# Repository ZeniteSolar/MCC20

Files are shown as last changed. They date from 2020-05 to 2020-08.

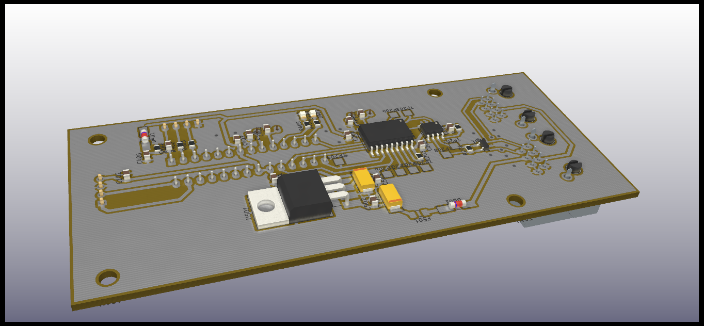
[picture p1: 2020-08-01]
hardware/IMG/3DDOWN.png

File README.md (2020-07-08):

# MCC20
**M**ódulo **C**ontrolador de **C**arga 2020  
Embarcação Guarapuvu II  
Equipe Zênite Solar  

### Sobre

Este módulo é responsável por gerenciar o carregamento da bateria e a operação do painel no seu ponto de maxima potencia 

#### Requisitos e Abordagens
1. Encontrar o ponto de maxima potencia (MPP) do painel solar
    - Utilizar a tecnica perturbar e observar (p&o) para achar o MPP
    - Ao iniciar barrer o duty cicle para iniciar no MPP
    - Se a potencia for 0 fazer o barrido novamente 
2. Medir a Potencia do painel
    - Usar um ina826 para medir a tensao do painel
    - Usar um ina240 para medir a corrente do painel
    
3. Eficiencia energetica
    - Indutores
        - Utilizar fios em paralelo para diminuir o *skin effect*
        - Utilizar indutor acoplado (não implementado)
    - Capacitores
        - Utilizar capacitores SMD com baixa ESR
    - Chaves
        - Utilizar snubber para amortecer oscilações e picos de tensão
        - Utilizar chaves com baixa Rdson e rapidas
        - Utilizar conversor sincrono (não implementado)
    - Frequencia
        - Utilizar frequencia que tenha uma boa relação entre perdas nas chaves e volume do onversor
    - Layout
        - Baixa indutancia no braço (entre chaves)
        - Trilhas curtas
    - Snubber
        - Equilibrio entre sobre-tensão nas chaves e potencia dissipada
4. Robustez
    - Chaves em regime seguro
        - Snubber
        - Layout
    - Proteção *under load* (nao implementado)
    - Capacitores em regime seguro
        - Tensao maxima >Vpan+Vbat
    - Tolerancia termica
        - Projetar assumindo que a temperatura ambiente é 50°
    - Layout simples de montar por metodo artesanal (transferencia termica)

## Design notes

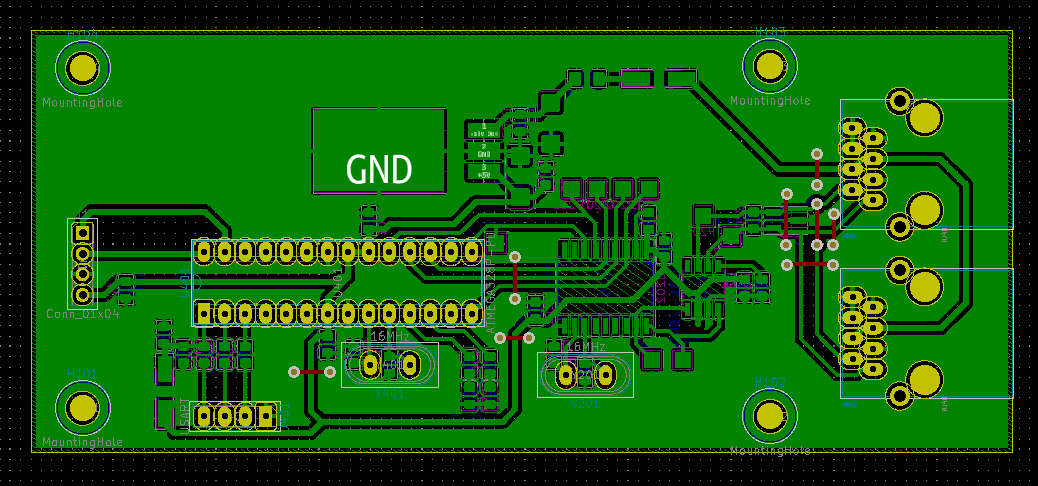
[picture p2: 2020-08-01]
hardware/IMG/layout.png

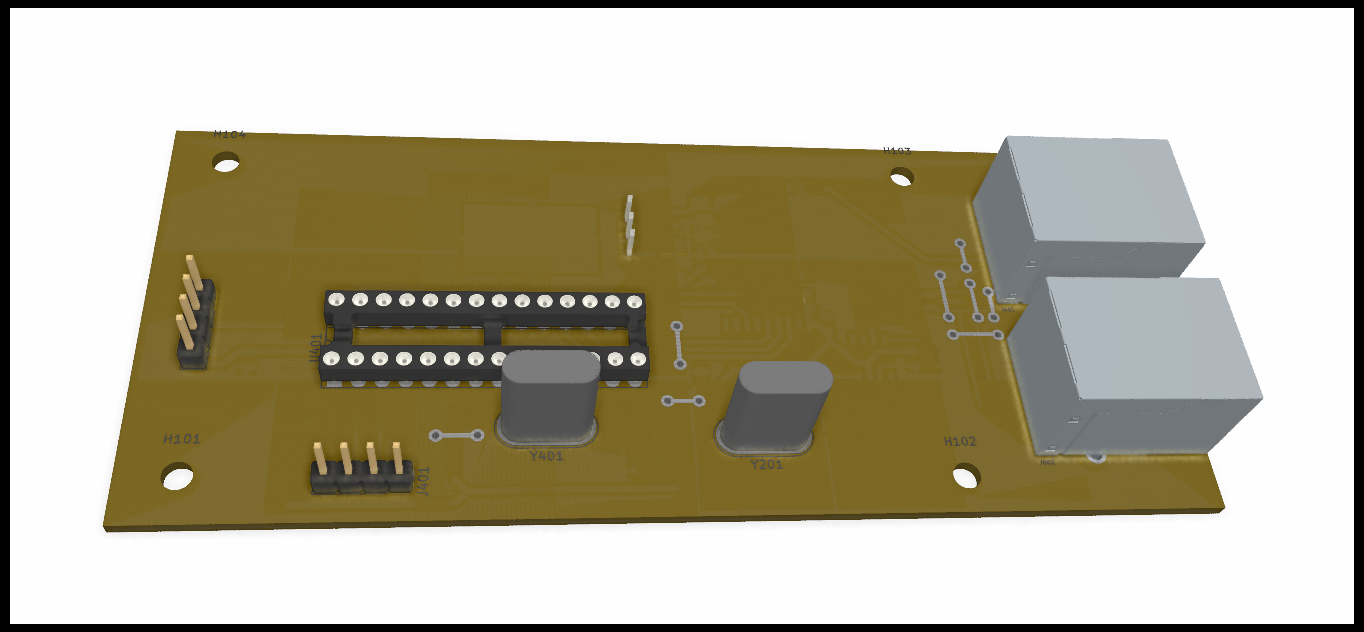
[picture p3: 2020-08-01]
hardware/IMG/3DUP.png

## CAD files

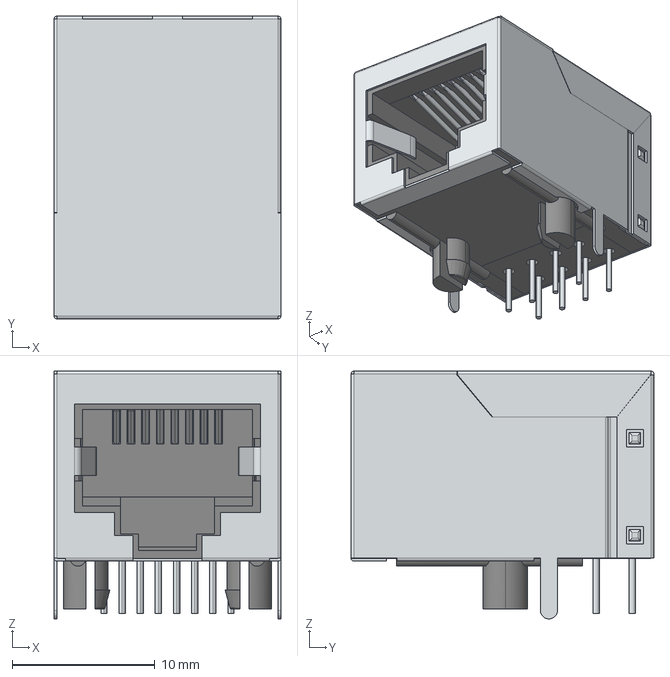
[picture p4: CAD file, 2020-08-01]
hardware/rj45.step
15.9 x 21.2 x 17.3 mm

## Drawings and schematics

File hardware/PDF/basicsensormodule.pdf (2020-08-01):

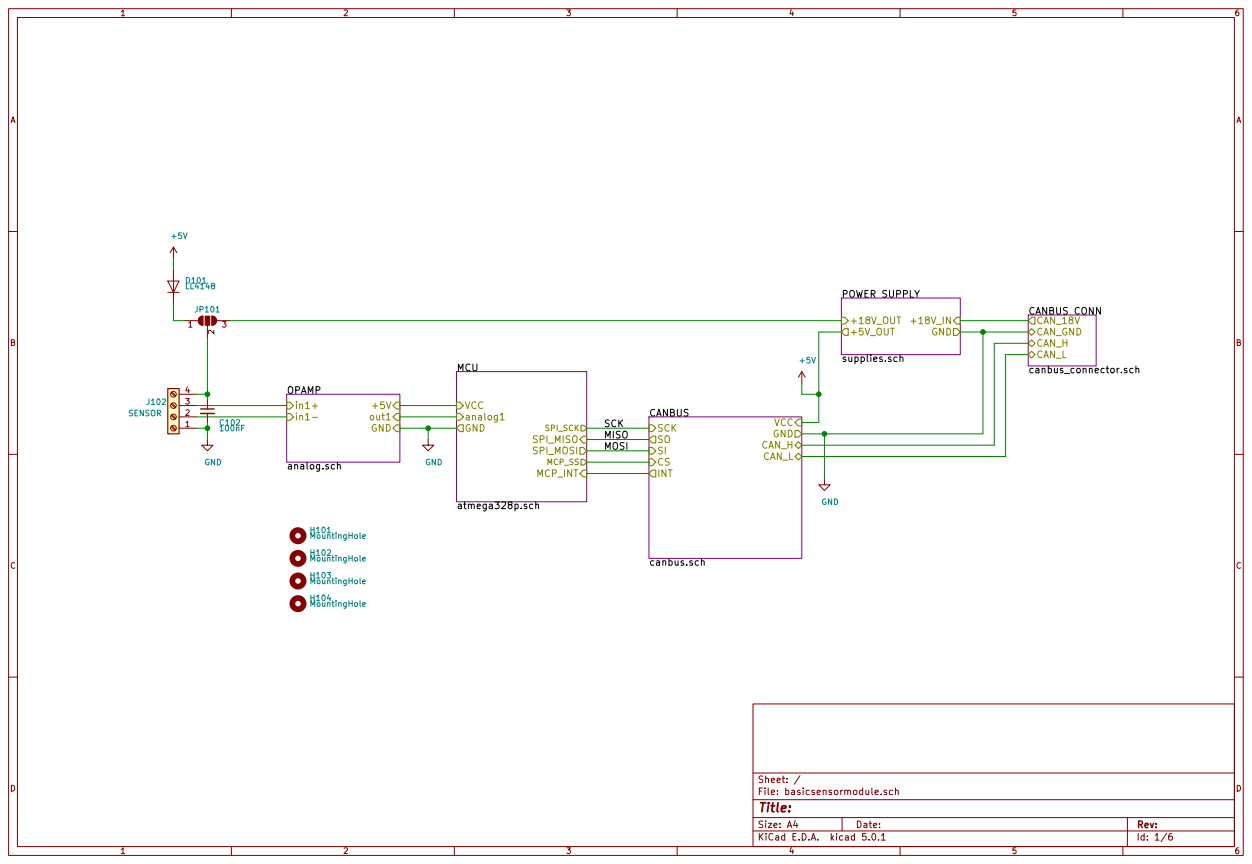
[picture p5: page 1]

Id: 1/6 Title: File: basicsensormodule.sch Sheet: / CANBUS
SCK
canbus.sch SI

MISO
MOSI

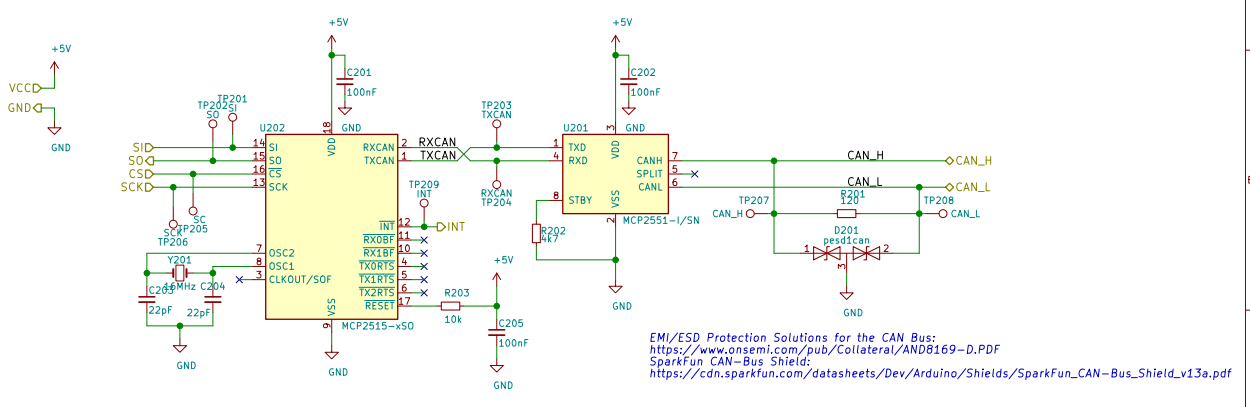
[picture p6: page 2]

https://cdn.sparkfun.com/datasheets/Dev/Arduino/Shields/SparkFun_CAN-Bus_Shield_v13a.pdf TP203 TXCAN

3 RXD 4 SPLIT 5 CANL 6 CANH 7 STBY 8 U201 MCP2551-I/SN TXCAN
RXCAN

EMI/ESD Protection Solutions for the CAN Bus:
https://www.onsemi.com/pub/Collateral/AND8169-D.PDF
SparkFun CAN-Bus Shield:

Id: 2/6 Title: File: canbus.sch Sheet: /CANBUS/

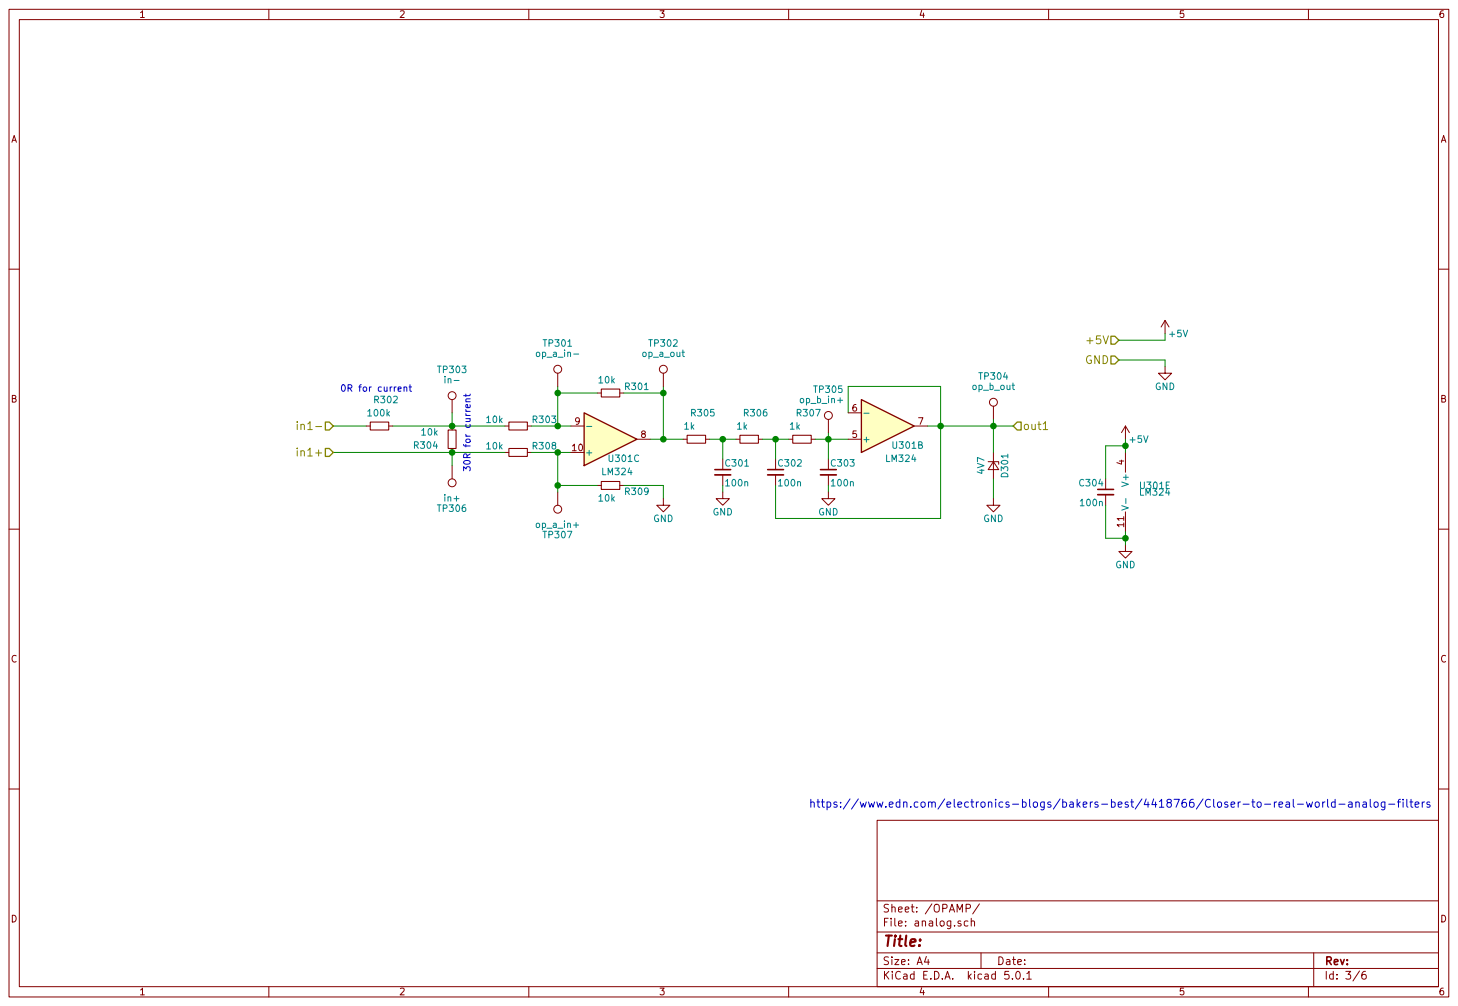
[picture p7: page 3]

https://www.edn.com/electronics-blogs/bakers-best/4418766/Closer-to-real-world-analog-filters R305

File: analog.sch Sheet: /OPAMP/
Id: 3/6 Title:

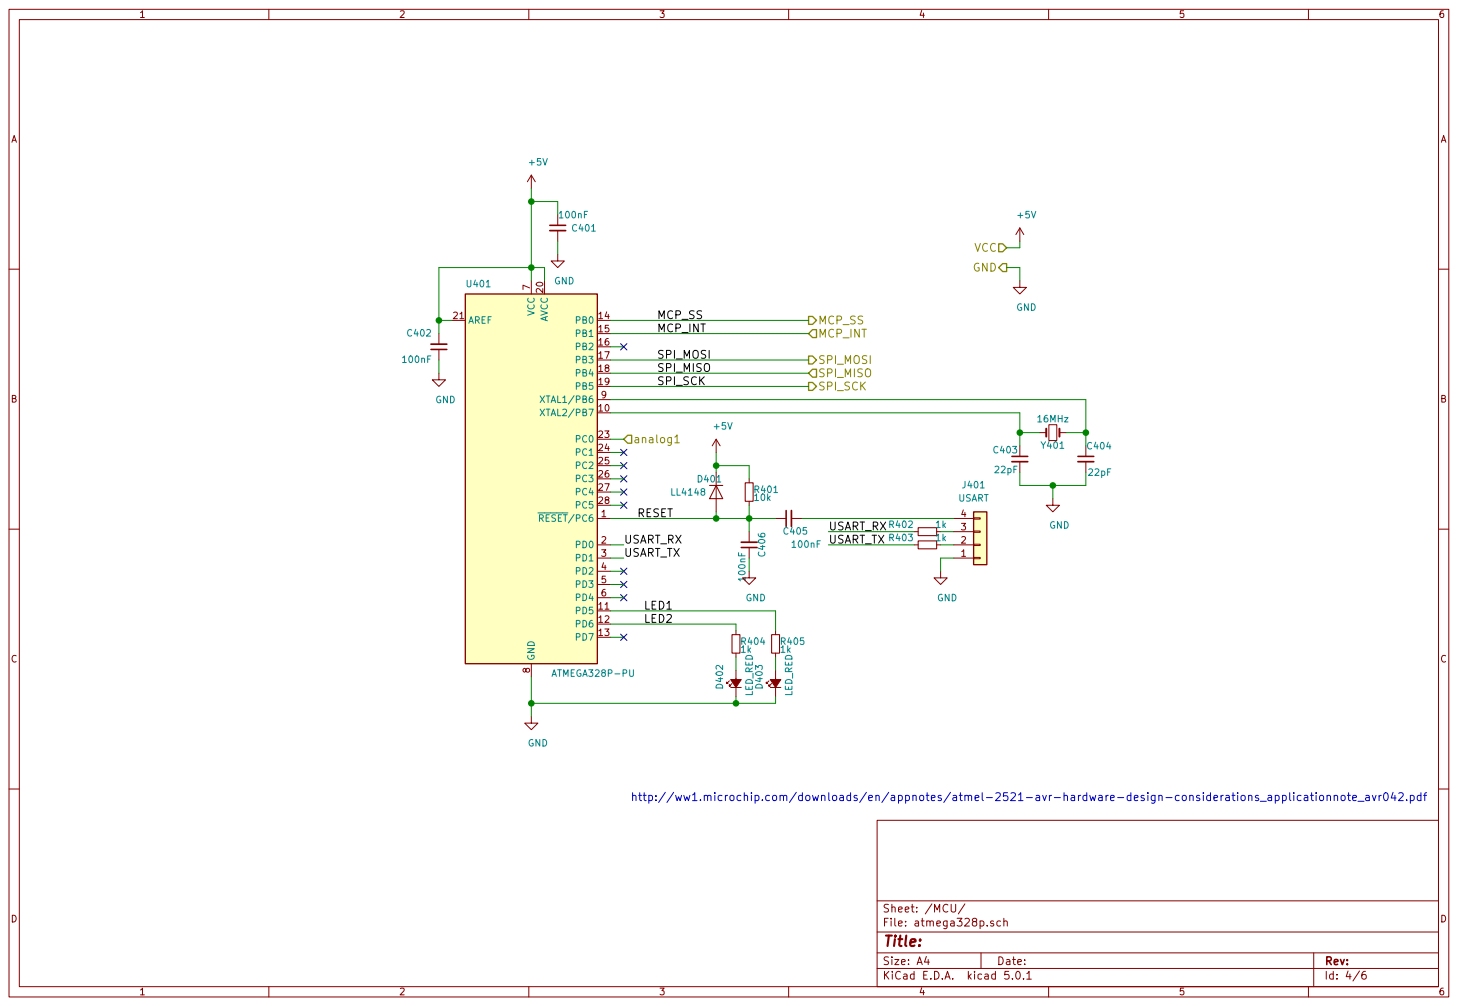
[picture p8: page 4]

File: atmega328p.sch Sheet: /MCU/
Id: 4/6 Title:

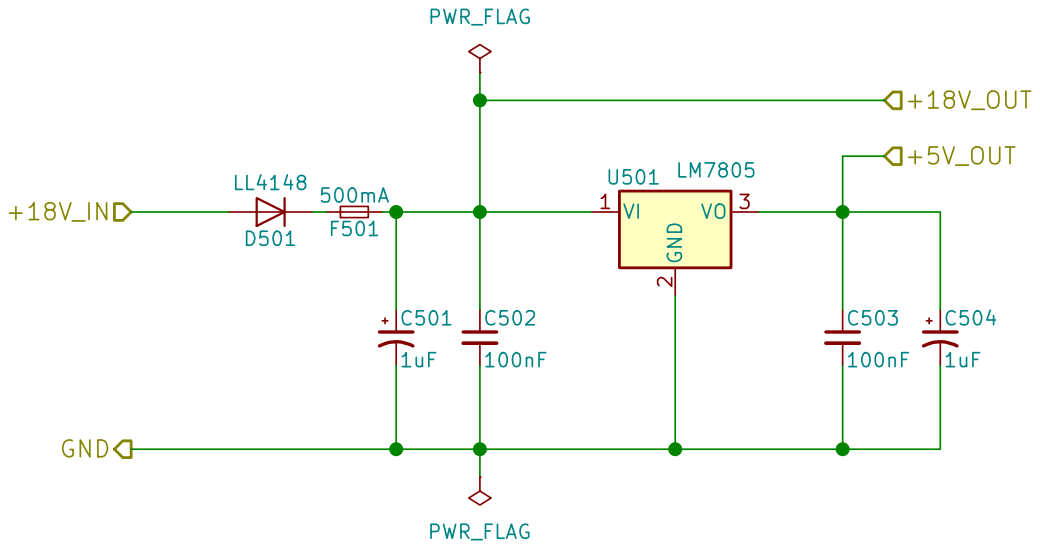
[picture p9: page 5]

File: supplies.sch Sheet: /POWER SUPPLY/
Id: 5/6 Title:

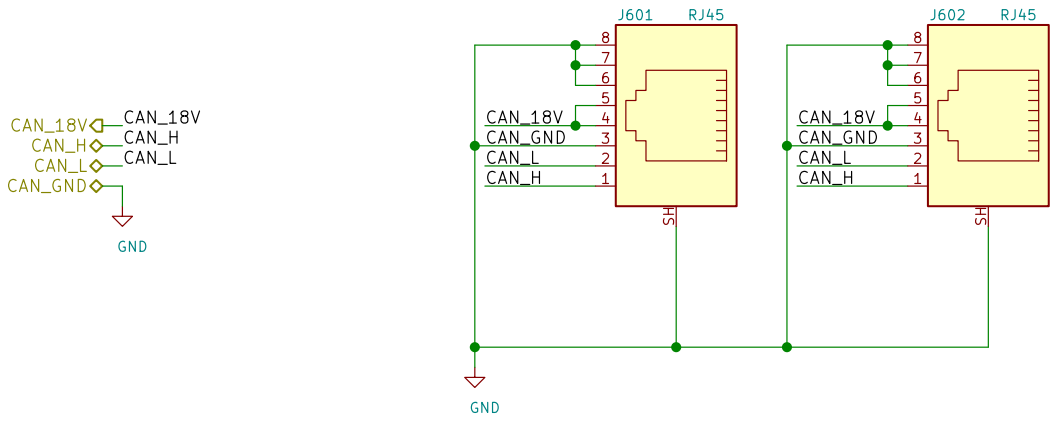
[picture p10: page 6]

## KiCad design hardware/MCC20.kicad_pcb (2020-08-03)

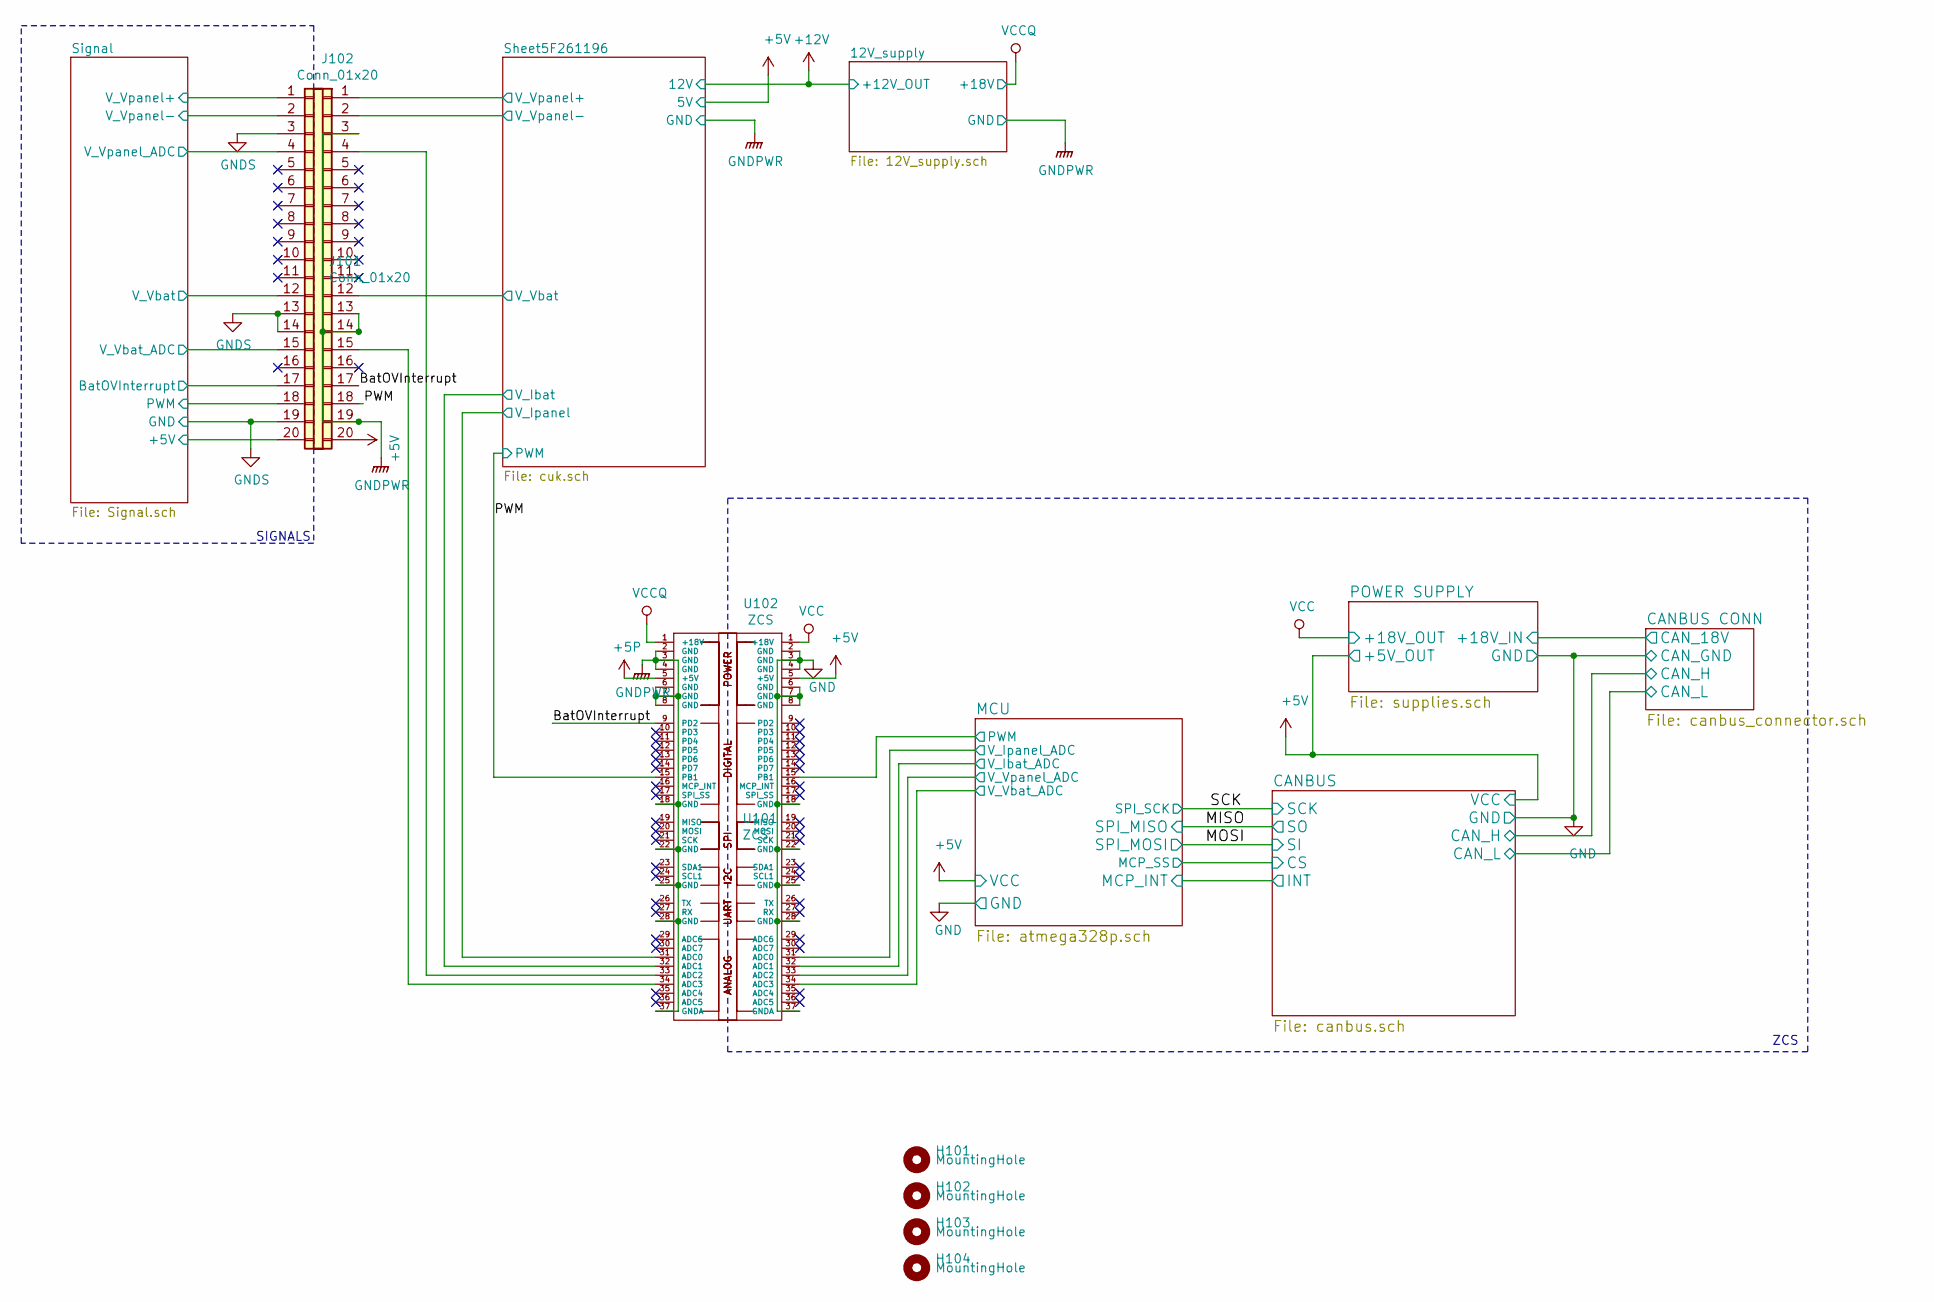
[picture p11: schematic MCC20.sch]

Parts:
H101, H102, H103, H104: MountingHole; MountingHole_3.2mm_M3
J101: Conn_01x20; PinHeader_1x20_P2.54mm_Horizontal
J102: Conn_01x20; PinSocket_1x20_P2.54mm_Vertical_SMD_Pin1Left
U101, U102: ZCS; ZCS18

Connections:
+5P: U101.5 (+5V)
+5V: J102.20, U102.5 (+5V); also elsewhere on the board
+5VA: J101.20; also elsewhere on the board
/BatOVInterrupt: J102.17, U101.9 (PD2)
/MCU/PWM: U102.15 (PB1); also elsewhere on the board
/MCU/V_Ibat_ADC: U102.32 (ADC1); also elsewhere on the board
/MCU/V_Ipanel_ADC: U102.31 (ADC0); also elsewhere on the board
/MCU/V_Vbat_ADC: U102.34 (ADC3); also elsewhere on the board
/MCU/V_Vpanel_ADC: U102.33 (ADC2); also elsewhere on the board
/PWM: J102.18, U101.15 (PB1); also elsewhere on the board
/Sheet5F261196/V_Ibat: U101.32 (ADC1); also elsewhere on the board
/Sheet5F261196/V_Ipanel: U101.31 (ADC0); also elsewhere on the board
/Sheet5F261196/V_Vbat: J102.12; also elsewhere on the board
/Sheet5F261196/V_Vpanel+: J102.1; also elsewhere on the board
/Sheet5F261196/V_Vpanel-: J102.2; also elsewhere on the board
/Signal/BatOVInterrupt: J101.17; also elsewhere on the board
/Signal/PWM: J101.18; also elsewhere on the board
/Signal/V_Vbat: J101.12; also elsewhere on the board
/Signal/V_Vbat_ADC: J101.15; also elsewhere on the board
/Signal/V_Vpanel+: J101.1; also elsewhere on the board
/Signal/V_Vpanel-: J101.2; also elsewhere on the board
/Signal/V_Vpanel_ADC: J101.4; also elsewhere on the board
GND: J102.3, J102.13, J102.14, J102.19, U101.2 (GND), U101.3 (GND), U101.4 (GND), U101.6 (GND), U101.7 (GND), U101.8 (GND), U101.18 (GND), U101.22 (GND), U101.25 (GND), U101.28 (GND), U101.37 (GNDA), U102.2 (GND), U102.3 (GND), U102.4 (GND), U102.6 (GND), U102.7 (GND), U102.8 (GND), U102.18 (GND), U102.22 (GND), U102.25 (GND), U102.28 (GND), U102.37 (GNDA); also elsewhere on the board
GNDA: J101.3, J101.13, J101.14, J101.19; also elsewhere on the board
unnamed: J102.4, U101.33 (ADC2)
unnamed: J102.15, U101.34 (ADC3)
VCC: U102.1 (+18V); also elsewhere on the board
VCCQ: U101.1 (+18V); also elsewhere on the board

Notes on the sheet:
ZCS
SIGNALS

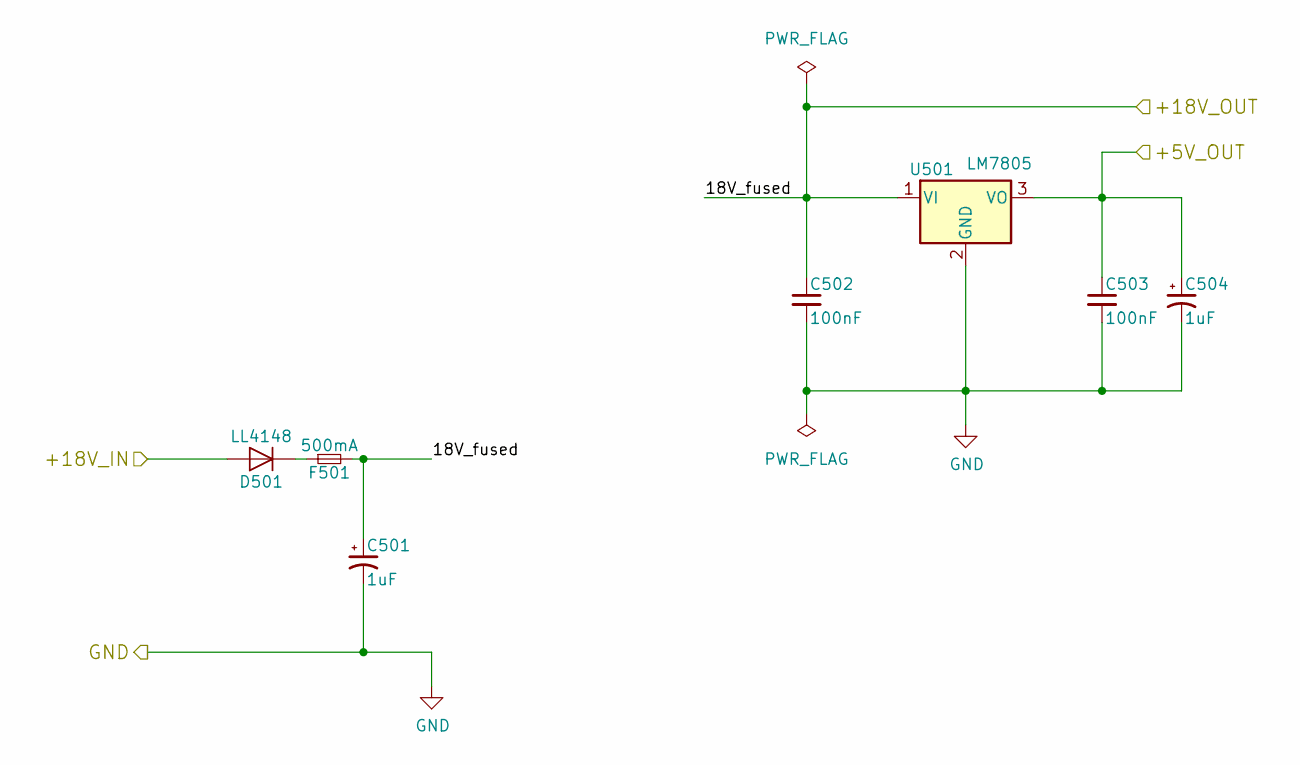
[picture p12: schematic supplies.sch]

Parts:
C501, C504: 1uF; CP_EIA-6032-20_AVX-F_Pad2.25x2.35mm_HandSolder
C502, C503: 100nF; C_0805_2012Metric_Pad1.15x1.40mm_HandSolder
D501: LL4148; D_MiniMELF_Handsoldering
F501: 500mA; Fuse_1206_3216Metric_Pad1.42x1.75mm_HandSolder
U501: LM7805; TO-220-3_Horizontal_TabDown_SMD

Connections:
+5V: C503.1, C504.1, U501.3 (VO); also elsewhere on the board
/POWER SUPPLY/+18V_IN: D501.2 (A); also elsewhere on the board
GND: C501.2, C502.2, C503.2, C504.2, U501.2 (GND); also elsewhere on the board
unnamed: D501.1 (K), F501.1
VCC: C501.1, C502.1, F501.2, U501.1 (VI); also elsewhere on the board

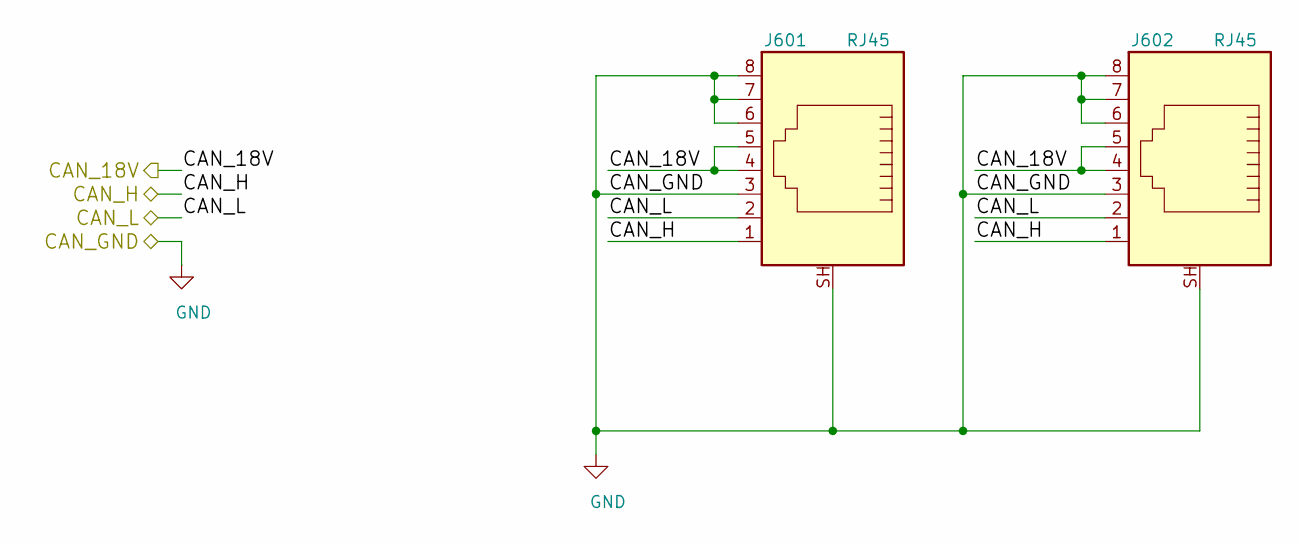
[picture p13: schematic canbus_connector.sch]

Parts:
J601, J602: RJ45; RJ45_YH59_01

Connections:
/CANBUS CONN/CAN_H: J601.1, J602.1; also elsewhere on the board
/CANBUS CONN/CAN_L: J601.2, J602.2; also elsewhere on the board
/POWER SUPPLY/+18V_IN: J601.4, J601.5, J602.4, J602.5; also elsewhere on the board
GND: J601.3, J601.6, J601.7, J601.8, J601.SH, J602.3, J602.6, J602.7, J602.8, J602.SH; also elsewhere on the board

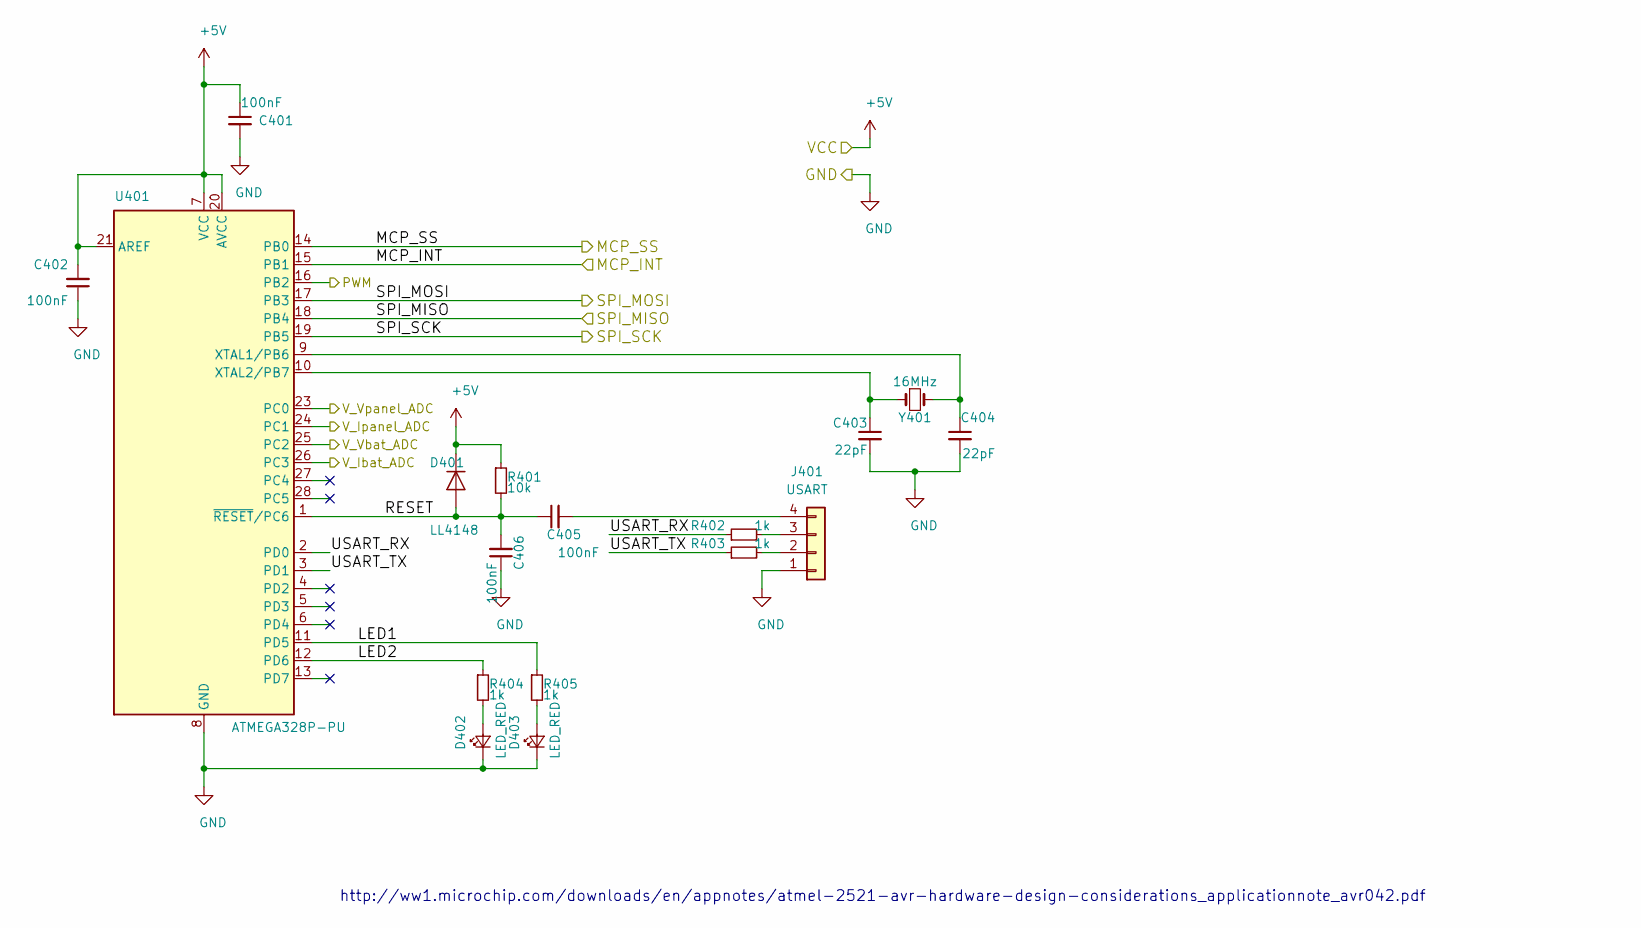
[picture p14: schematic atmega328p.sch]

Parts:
C401, C402, C405, C406: 100nF; C_0805_2012Metric_Pad1.15x1.40mm_HandSolder
C403, C404: 22pF; C_0805_2012Metric_Pad1.15x1.40mm_HandSolder
D401: LL4148; D_MiniMELF_Handsoldering
D402, D403: LED_RED; LED_0805_2012Metric_Pad1.15x1.40mm_HandSolder
J401: USART; PinHeader_1x04_P2.54mm_Vertical
R401: 10k; R_0805_2012Metric_Pad1.15x1.40mm_HandSolder
R402, R403, R404, R405: 1k; R_0805_2012Metric_Pad1.15x1.40mm_HandSolder
U401: ATMEGA328P-PU; DIP-28_W7.62mm_Socket
Y401: 16MHz; Crystal_HC49-U_Vertical

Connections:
+5V: C401.1, C402.2, D401.1 (K), R401.1, U401.7 (VCC), U401.20 (AVCC), U401.21 (AREF); also elsewhere on the board
/CANBUS/CS: U401.14 (PB0); also elsewhere on the board
/CANBUS/INT: U401.15 (PB1); also elsewhere on the board
/MCU/LED1: R405.1, U401.11 (PD5)
/MCU/LED2: R404.1, U401.12 (PD6)
/MCU/PWM: U401.16 (PB2); also elsewhere on the board
/MCU/RESET: C405.1, C406.2, D401.2 (A), R401.2, U401.1 (~RESET~/PC6)
/MCU/USART_RX: R402.1, U401.2 (PD0)
/MCU/USART_TX: R403.1, U401.3 (PD1)
/MCU/V_Ibat_ADC: U401.26 (PC3); also elsewhere on the board
/MCU/V_Ipanel_ADC: U401.24 (PC1); also elsewhere on the board
/MCU/V_Vbat_ADC: U401.25 (PC2); also elsewhere on the board
/MCU/V_Vpanel_ADC: U401.23 (PC0); also elsewhere on the board
/MISO: U401.18 (PB4); also elsewhere on the board
/MOSI: U401.17 (PB3); also elsewhere on the board
/SCK: U401.19 (PB5); also elsewhere on the board
GND: C401.2, C402.1, C403.2, C404.2, C406.1, D402.1 (K), D403.1 (K), J401.1, U401.8 (GND), U401.22 (GND); also elsewhere on the board
unnamed: C403.1, U401.10 (XTAL2/PB7), Y401.1
unnamed: C404.1, U401.9 (XTAL1/PB6), Y401.2
unnamed: C405.2, J401.4
unnamed: D402.2 (A), R404.2
unnamed: D403.2 (A), R405.2
unnamed: J401.2, R403.2
unnamed: J401.3, R402.2

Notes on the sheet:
http://ww1.microchip.com/downloads/en/appnotes/atmel-2521-avr-hardware-design-considerations_applicationnote_avr042.pdf

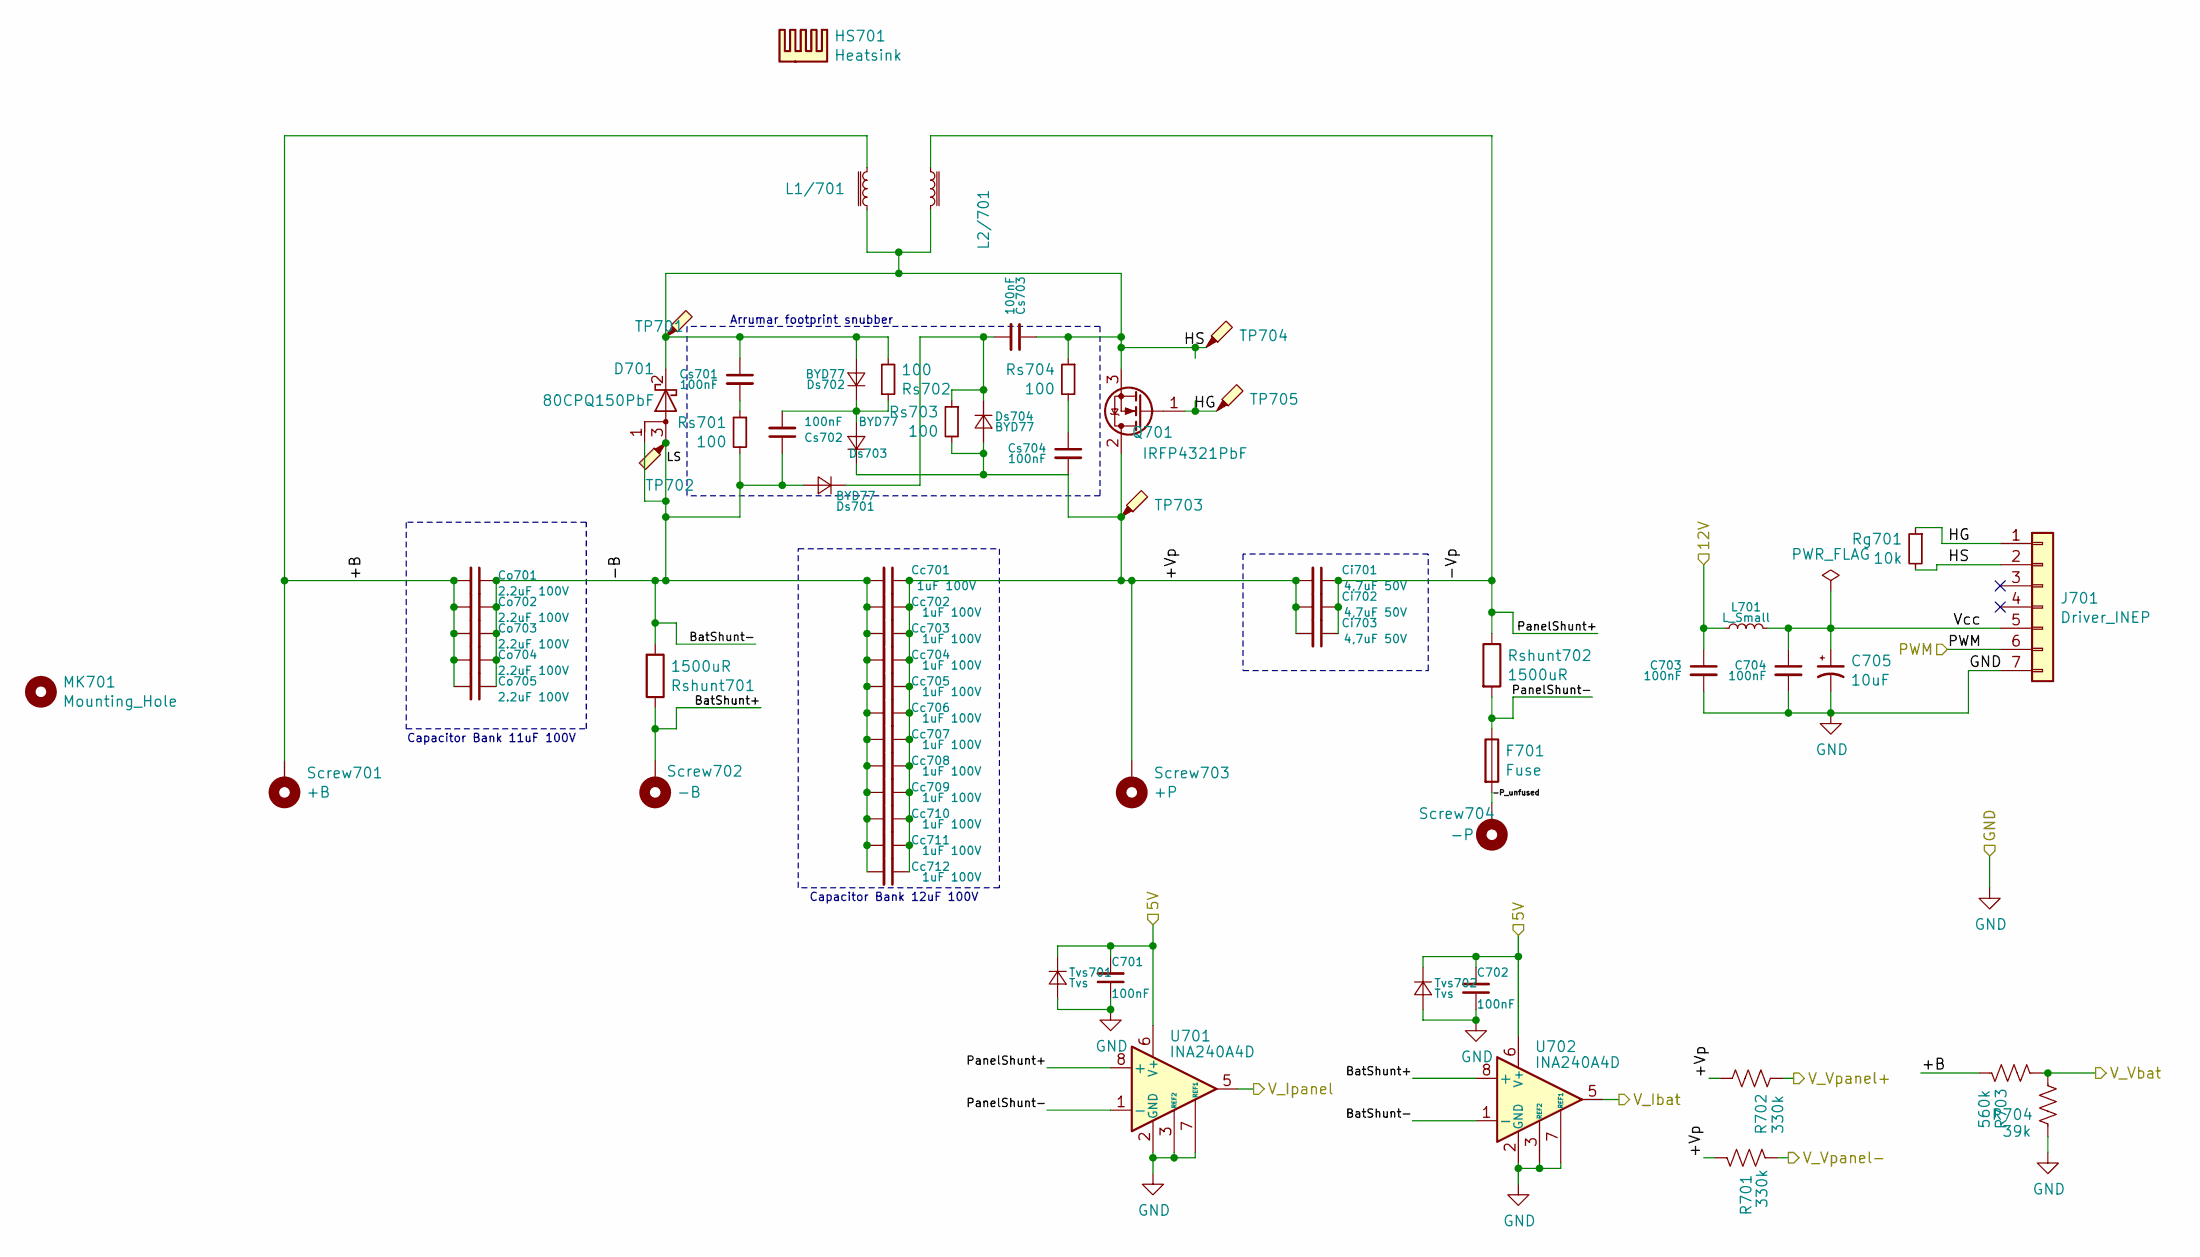
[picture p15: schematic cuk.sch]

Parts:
C701, C702, C703, C704: 100nF; C_0805_2012Metric_Pad1.15x1.40mm_HandSolder
C705: 10uF; C_0805_2012Metric_Pad1.15x1.40mm_HandSolder
Cc701, Cc702, Cc703, Cc704, Cc705, Cc706, Cc707, Cc708, Cc709, Cc710, Cc711, Cc712: 1uF 100V; C_1206_3216Metric_Pad1.42x1.75mm_HandSolder
Ci701, Ci702, Ci703: 4,7uF 50V; C_1206_3216Metric_Pad1.42x1.75mm_HandSolder
Co701, Co702, Co703, Co704, Co705: 2.2uF 100V; C_1206_3216Metric_Pad1.42x1.75mm_HandSolder
Cs701, Cs702, Cs703, Cs704: 100nF; C_1206_3216Metric_Pad1.42x1.75mm_HandSolder
D701: 80CPQ150PbF; TO-247-3_Horizontal_TabUp
Ds701, Ds702, Ds703, Ds704: BYD77; D_MELF_Handsoldering
F701: Fuse; Porta_Fusivel
HS701: Heatsink; hs10425
J701: Driver_INEP; Driver_(INEP)_SMD
L1/701, L2/701: L_Core_Iron_Small; Inductor_Nocoupled
L701: L_Small; L_0805_2012Metric_Pad1.15x1.40mm_HandSolder
MK701: Mounting_Hole; MountingHole_2.2mm_M2_Pad
Q701: IRFP4321PbF; TO-247-3_Horizontal_TabUp
R701, R702: 330k; R_0805_2012Metric_Pad1.15x1.40mm_HandSolder
R703: 560k; R_0805_2012Metric_Pad1.15x1.40mm_HandSolder
R704: 39k; R_0805_2012Metric_Pad1.15x1.40mm_HandSolder
Rg701: 10k; R_0805_2012Metric_Pad1.15x1.40mm_HandSolder
Rs701, Rs702, Rs703, Rs704: 100; R_2512_6332Metric_Pad1.52x3.35mm_HandSolder
Rshunt701, Rshunt702: 1500uR; PML100HZPJV0L5
Screw701: +B; MountingHole_5mm_Pad
Screw702: -B; MountingHole_5mm_Pad
Screw703: +P; MountingHole_5mm_Pad
Screw704: -P; MountingHole_5mm_Pad
TP701, TP702, TP703, TP704, TP705: TestPoint_Probe; TestPoint_Pad_D1.0mm
Tvs701, Tvs702: Tvs; D_0805_2012Metric_Castellated
U701, U702: INA240A4D; SOIC-8_3.9x4.9mm_P1.27mm

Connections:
+5V: C701.2, C702.2, Tvs701.1 (K), Tvs702.1 (K), U701.6 (V+), U702.6 (V+); also elsewhere on the board
+12V: C703.1, L701.1; also elsewhere on the board
/PWM: J701.6; also elsewhere on the board
/Sheet5F261196/+B: Co701.2, Co702.2, Co703.2, Co704.2, Co705.2, L1/701.2, R703.1, Screw701.1
/Sheet5F261196/+Vp: Cc701.1, Cc702.1, Cc703.1, Cc704.1, Cc705.1, Cc706.1, Cc707.1, Cc708.1, Cc709.1, Cc710.1, Cc711.1, Cc712.1, Ci701.2, Ci702.2, Ci703.2, Cs704.2, Ds703.1 (K), Ds704.2 (A), Q701.2 (D), R701.1, R702.2, Rs703.2, Screw703.1, TP703.1
/Sheet5F261196/-B: Cc701.2, Cc702.2, Cc703.2, Cc704.2, Cc705.2, Cc706.2, Cc707.2, Cc708.2, Cc709.2, Cc710.2, Cc711.2, Cc712.2, Co701.1, Co702.1, Co703.1, Co704.1, Co705.1, Cs702.1, D701.1 (A), D701.3 (A), Ds701.2 (A), Rs701.2, Rshunt701.2, TP702.1, U702.1 (-)
/Sheet5F261196/-P_unfused: F701.2, Screw704.1
/Sheet5F261196/-Vp: Ci701.1, Ci702.1, Ci703.1, L2/701.1, Rshunt702.1, U701.8 (+)
/Sheet5F261196/BatShunt+: Rshunt701.1, Screw702.1, U702.8 (+)
/Sheet5F261196/HG: J701.1, Q701.1 (G), Rg701.1, TP705.1
/Sheet5F261196/HS: Cs701.1, Cs703.1, D701.2 (K), Ds702.2 (A), J701.2, L1/701.1, L2/701.2, Q701.3 (S), Rg701.2, Rs702.2, Rs704.1, TP701.1, TP704.1
/Sheet5F261196/PanelShunt-: F701.1, Rshunt702.2, U701.1 (-)
/Sheet5F261196/V_Ibat: U702.5; also elsewhere on the board
/Sheet5F261196/V_Ipanel: U701.5; also elsewhere on the board
/Sheet5F261196/V_Vbat: R703.2, R704.2; also elsewhere on the board
/Sheet5F261196/V_Vpanel+: R702.1; also elsewhere on the board
/Sheet5F261196/V_Vpanel-: R701.2; also elsewhere on the board
/Sheet5F261196/Vcc: C704.1, C705.1, J701.5, L701.2
GND: C701.1, C702.1, C703.2, C704.2, C705.2, J701.7, R704.1, Tvs701.2 (A), Tvs702.2 (A), U701.2 (GND), U701.3 (REF2), U701.4 (GND), U701.7 (REF1), U702.2 (GND), U702.3 (REF2), U702.4 (GND), U702.7 (REF1); also elsewhere on the board
unnamed: Cs701.2, Rs701.1
unnamed: Cs702.2, Ds702.1 (K), Ds703.2 (A), Rs702.1
unnamed: Cs703.2, Ds701.1 (K), Ds704.1 (K), Rs703.1
unnamed: Cs704.1, Rs704.2

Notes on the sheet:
Capacitor Bank 12uF 100V
Capacitor Bank 11uF 100V
Arrumar footprint snubber

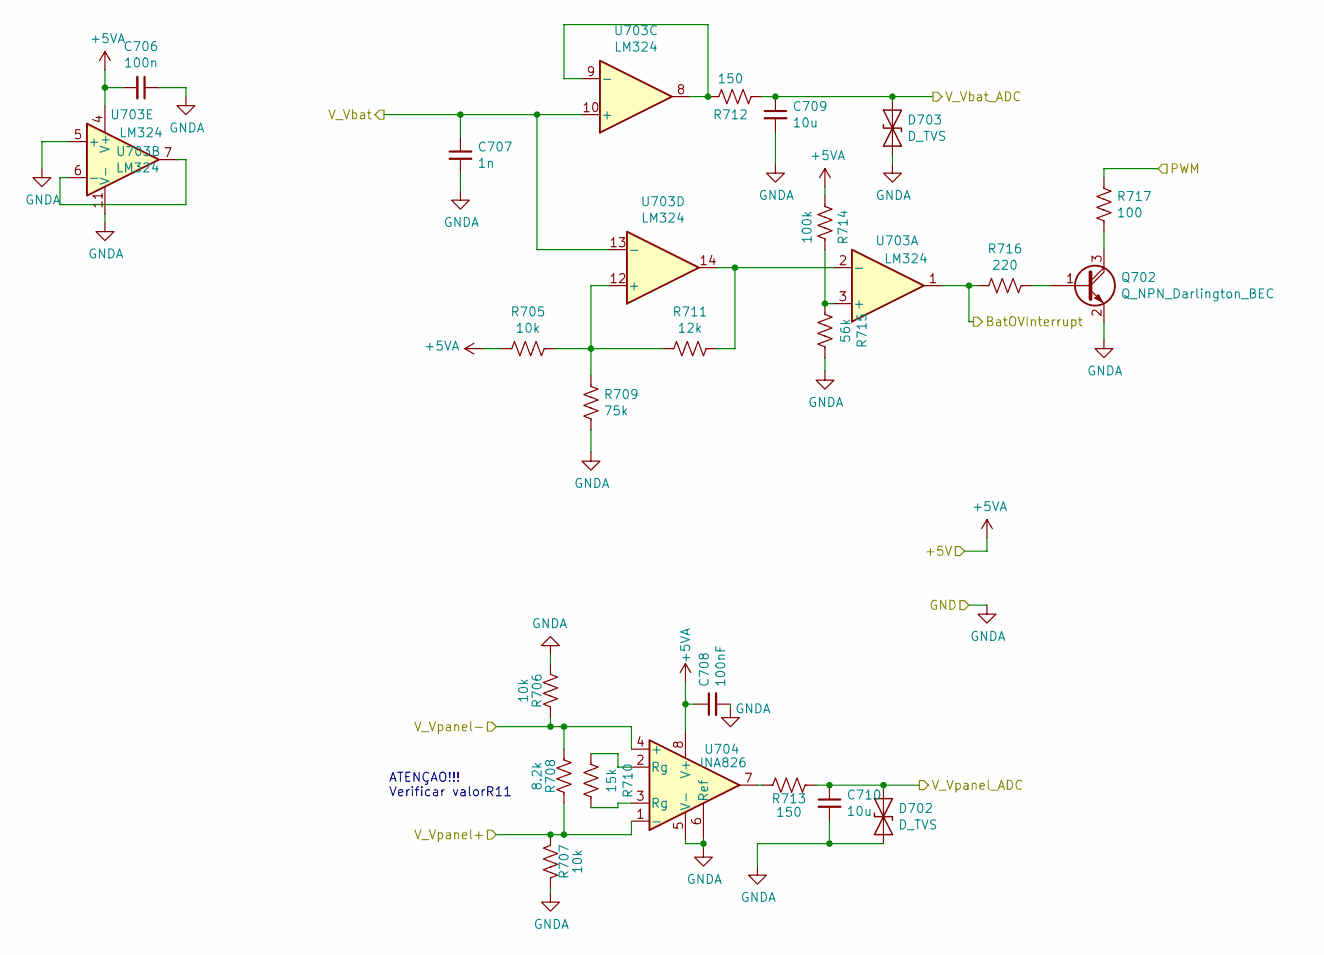
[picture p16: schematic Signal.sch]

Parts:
C706: 100n; C_0805_2012Metric_Pad1.15x1.40mm_HandSolder
C707: 1n; C_0805_2012Metric_Pad1.15x1.40mm_HandSolder
C708: 100nF; C_0805_2012Metric_Pad1.15x1.40mm_HandSolder
C709, C710: 10u; C_2512_6332Metric_Pad1.52x3.35mm_HandSolder
D702, D703: D_TVS; D_0805_2012Metric_Castellated
Q702: Q_NPN_Darlington_BEC; SOT-23
R705, R706, R707: 10k; R_0805_2012Metric_Pad1.15x1.40mm_HandSolder
R708: 8.2k; R_0805_2012Metric_Pad1.15x1.40mm_HandSolder
R709: 75k; R_0805_2012Metric_Pad1.15x1.40mm_HandSolder
R710: 15k; R_0805_2012Metric_Pad1.15x1.40mm_HandSolder
R711: 12k; R_0805_2012Metric_Pad1.15x1.40mm_HandSolder
R712, R713: 150; R_0805_2012Metric_Pad1.15x1.40mm_HandSolder
R714: 100k; R_0805_2012Metric_Pad1.15x1.40mm_HandSolder
R715: 56k; R_0805_2012Metric_Pad1.15x1.40mm_HandSolder
R716: 220; R_0805_2012Metric_Pad1.15x1.40mm_HandSolder
R717: 100; R_0805_2012Metric_Pad1.15x1.40mm_HandSolder
U703: LM324; SOIC-14_3.9x8.7mm_P1.27mm
U704: INA826; SOIC-8_3.9x4.9mm_P1.27mm

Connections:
+5VA: C706.2, C708.1, R705.2, R714.2, U703.4 (V+), U704.8 (V+); also elsewhere on the board
/Signal/BatOVInterrupt: R716.2, U703.1; also elsewhere on the board
/Signal/PWM: R717.1; also elsewhere on the board
/Signal/V_Vbat: C707.1, U703.10 (+), U703.13 (-); also elsewhere on the board
/Signal/V_Vbat_ADC: C709.1, D703.1 (A1), R712.2; also elsewhere on the board
/Signal/V_Vpanel+: R707.2, R708.1, U704.1 (-); also elsewhere on the board
/Signal/V_Vpanel-: R706.1, R708.2, U704.4 (+); also elsewhere on the board
/Signal/V_Vpanel_ADC: C710.1, D702.1 (A1), R713.1; also elsewhere on the board
GNDA: C706.1, C707.2, C708.2, C709.2, C710.2, D702.2 (A2), D703.2 (A2), Q702.2 (E), R706.2, R707.1, R709.1, R715.1, U703.5 (+), U703.11 (V-), U704.5 (V-), U704.6 (Ref); also elsewhere on the board
unnamed: Q702.1 (B), R716.1
unnamed: Q702.3 (C), R717.2
unnamed: R705.1, R709.2, R711.2, U703.12 (+)
unnamed: R710.1, U704.3 (Rg)
unnamed: R710.2, U704.2 (Rg)
unnamed: R711.1, U703.2 (-), U703.14
unnamed: R712.1, U703.8, U703.9 (-)
unnamed: R713.2, U704.7
unnamed: R714.1, R715.2, U703.3 (+)
unnamed: U703.6 (-), U703.7

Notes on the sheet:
ATENÇAO!!! Verificar valorR11

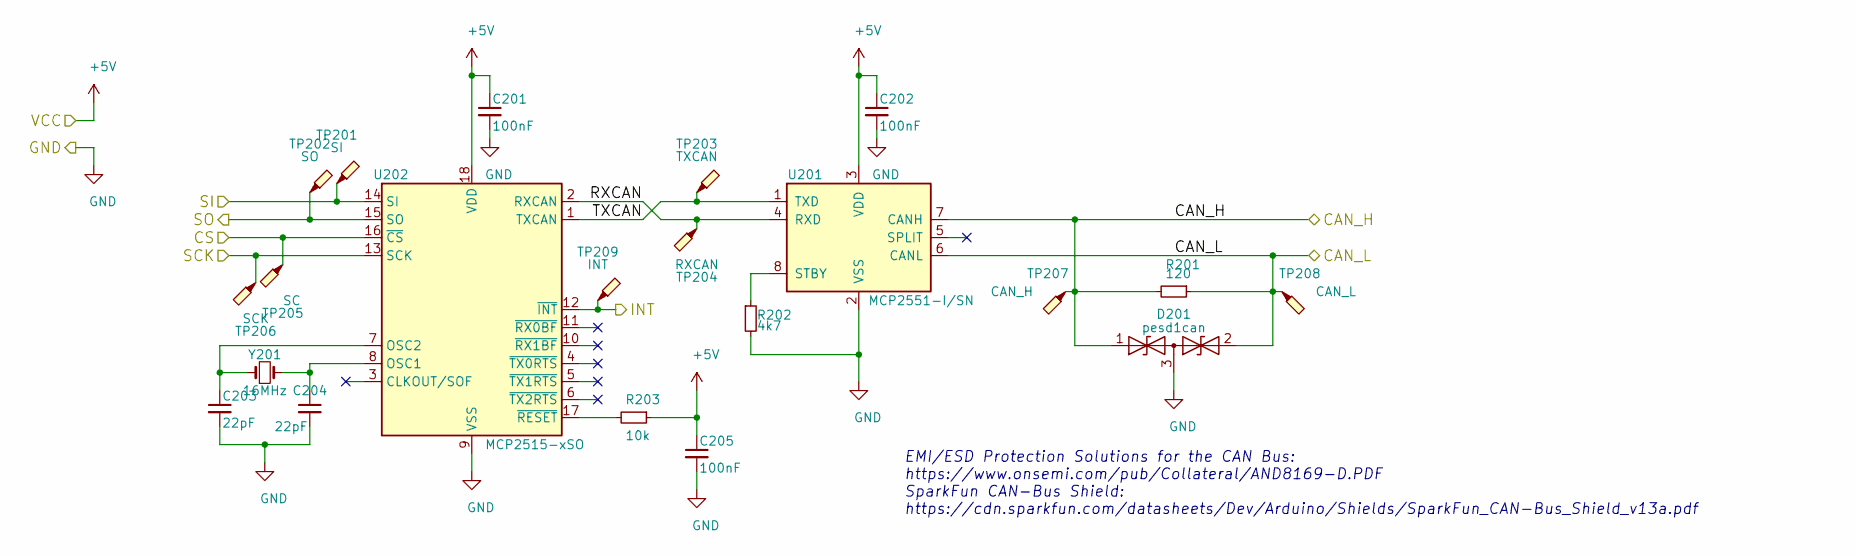
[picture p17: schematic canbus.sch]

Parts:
C201, C202, C205: 100nF; C_0805_2012Metric_Pad1.15x1.40mm_HandSolder
C203, C204: 22pF; C_0805_2012Metric_Pad1.15x1.40mm_HandSolder
D201: pesd1can; SOT-23_Handsoldering
R201: 120; R_0805_2012Metric_Pad1.15x1.40mm_HandSolder
R202: 4k7; R_0805_2012Metric_Pad1.15x1.40mm_HandSolder
R203: 10k; R_0805_2012Metric_Pad1.15x1.40mm_HandSolder
TP201: SI; TestPoint_Pad_2.0x2.0mm
TP202: SO; TestPoint_Pad_2.0x2.0mm
TP203: TXCAN; TestPoint_Pad_2.0x2.0mm
TP204: RXCAN; TestPoint_Pad_2.0x2.0mm
TP205: SC; TestPoint_Pad_2.0x2.0mm
TP206: SCK; TestPoint_Pad_2.0x2.0mm
TP207: CAN_H; TestPoint_Pad_2.0x2.0mm
TP208: CAN_L; TestPoint_Pad_2.0x2.0mm
TP209: INT; TestPoint_Pad_2.0x2.0mm
U201: MCP2551-I/SN; SOIC-8_3.9x4.9mm_P1.27mm
U202: MCP2515-xSO; SOIC-18W_7.5x11.6mm_P1.27mm
Y201: 16MHz; Crystal_HC49-U_Vertical

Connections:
+5V: C201.1, C202.1, C205.1, R203.1, U201.3 (VDD), U202.18 (VDD); also elsewhere on the board
/CANBUS CONN/CAN_H: D201.1 (A1), R201.2, TP207.1, U201.7 (CANH); also elsewhere on the board
/CANBUS CONN/CAN_L: D201.2 (A2), R201.1, TP208.1, U201.6 (CANL); also elsewhere on the board
/CANBUS/CS: TP205.1, U202.16 (~CS); also elsewhere on the board
/CANBUS/INT: TP209.1, U202.12 (~INT); also elsewhere on the board
/CANBUS/RXCAN: TP204.1, U201.4 (RXD), U202.2 (RXCAN)
/CANBUS/TXCAN: TP203.1, U201.1 (TXD), U202.1 (TXCAN)
/MISO: TP202.1, U202.15 (SO); also elsewhere on the board
/MOSI: TP201.1, U202.14 (SI); also elsewhere on the board
/SCK: TP206.1, U202.13 (SCK); also elsewhere on the board
GND: C201.2, C202.2, C203.2, C204.2, C205.2, D201.3 (common), R202.2, U201.2 (VSS), U202.9 (VSS); also elsewhere on the board
unnamed: C203.1, U202.7 (OSC2), Y201.1
unnamed: C204.1, U202.8 (OSC1), Y201.2
unnamed: R202.1, U201.8 (STBY)
unnamed: R203.2, U202.17 (~RESET)

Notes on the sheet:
EMI/ESD Protection Solutions for the CAN Bus: https://www.onsemi.com/pub/Collateral/AND8169-D.PDF SparkFun CAN-Bus Shield: https://cdn.sparkfun.com/datasheets/Dev/Arduino/Shields/SparkFun_CAN-Bus_Shield_v13a.pdf

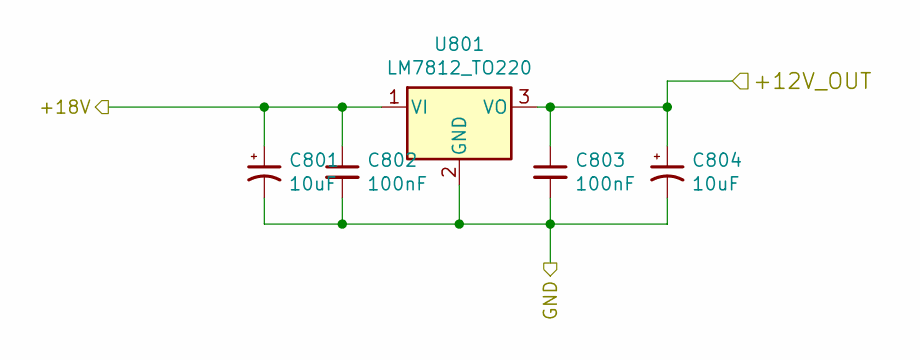
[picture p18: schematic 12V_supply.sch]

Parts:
C801, C804: 10uF; C_0805_2012Metric_Pad1.15x1.40mm_HandSolder
C802, C803: 100nF; C_0805_2012Metric_Pad1.15x1.40mm_HandSolder
U801: LM7812_TO220; TO-220-3_Horizontal_TabDown_SMD

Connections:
+12V: C803.1, C804.1, U801.3 (VO); also elsewhere on the board
GND: C801.2, C802.2, C803.2, C804.2, U801.2 (GND); also elsewhere on the board
VCCQ: C801.1, C802.1, U801.1 (VI); also elsewhere on the board

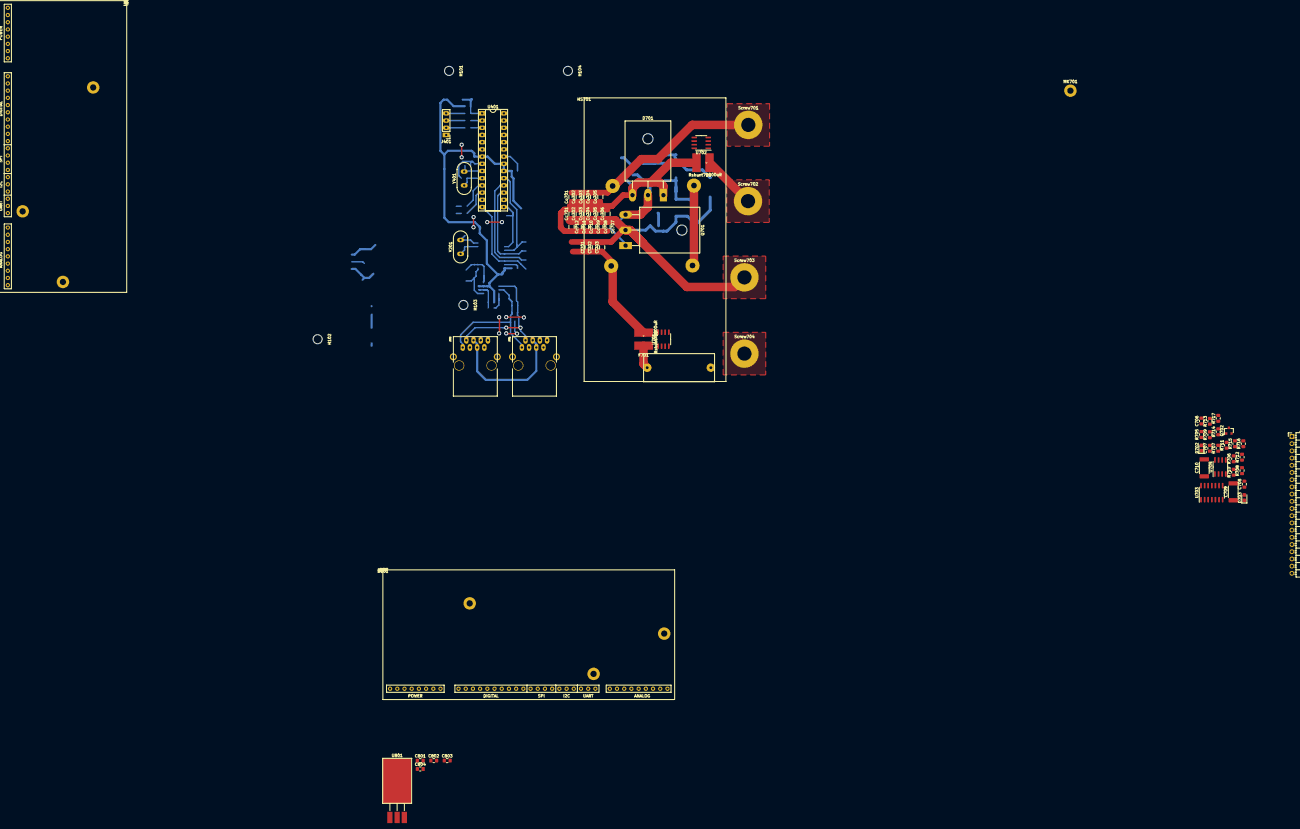
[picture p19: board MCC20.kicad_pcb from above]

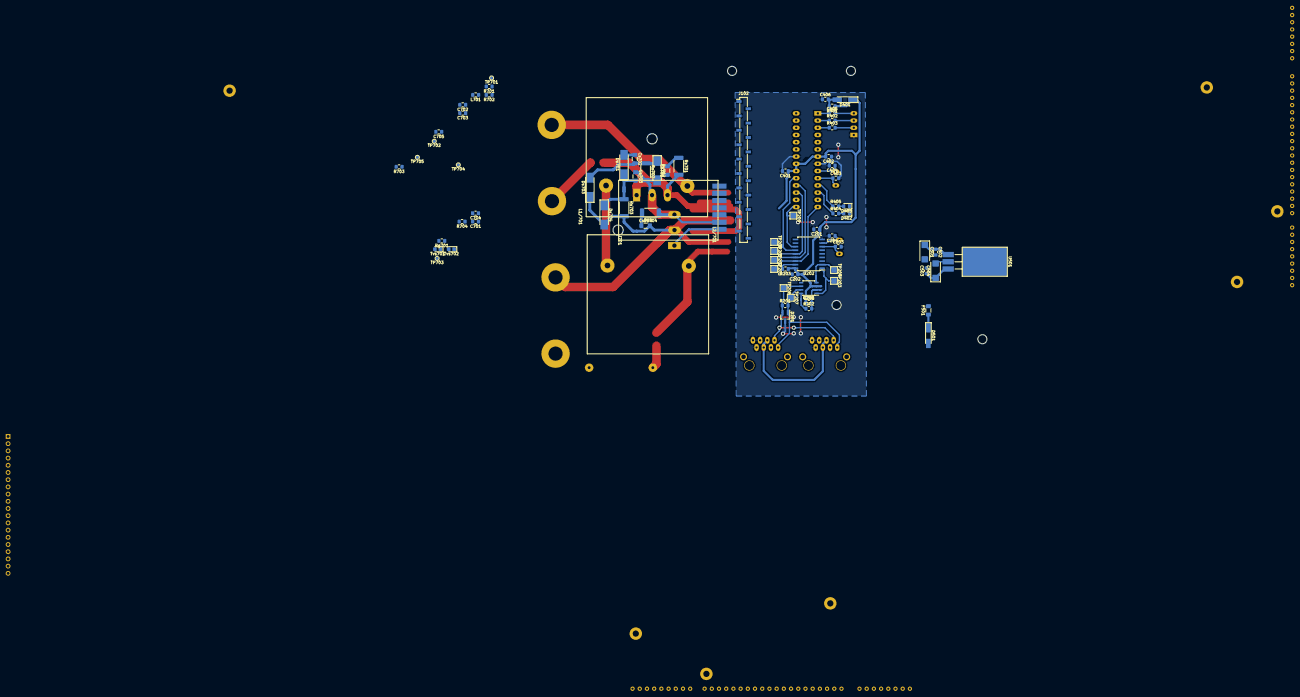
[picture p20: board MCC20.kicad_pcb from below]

Board: 2 copper layers, 149 parts (75 on the bottom side), 79 nets.

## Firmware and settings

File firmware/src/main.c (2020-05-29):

#include <math.h>
#include <stdio.h>
#include <stdlib.h>

#include "control.h"
#include "solvers.h"
#include "panel_model.h"
#include "socket.h"

extern unsigned char MPPT_STATE;

static inline double fun_circuit(double x, const double *params[])
{
  double Vpv, Ipv, Ro;

  Vpv = x;
  Ro = *params[0];
  Ipv = panel_model(Vpv,params);

  double F = Ipv * Ro - Vpv;

  return F;
}


int main(void)
{
  // Simulation runtime configuration
  const double end_time = 700e-3;
  const double delta_time = 1.0e-5;
  double time = 0;
  int ret = 0;

  // Bisect solver configuration
  double xmin = 0;
  double xmax = 1e3;
  double tol = 1e-6;
  unsigned int maxiter = 100;
  
  // Circuit configuration
  double Ro, Vpv, Ipv ,D ,M;
  double Rl = 5;

  // Panel configuration
  double Voc = 40;
  double Isc = 8;
  double G = 1000;

  const double *params[] = {&Ro, &Ipv, &Voc, &Isc, &G};
  
  // Socket configuration
  const char *simulation_output_socket = "simulation_output_socket";
  create_socket(simulation_output_socket);
  const unsigned int simulation_output_data_length = 5;
  const double *simulation_output_data[] = {&time, &Ro, &Vpv, &Ipv, &D};

  // Controller configuration
  set_mppt_initializing();

  printf("|-------------------------------------------------------------------|\n");
  printf("| %-9s| %-7s| %-7s| %-7s| %-7s| %-7s| %-7s| %-4s|\n", 
      "time", "Ro", "Ipv", "Vpv", "Vpv/Ipv", "Ppv","D","MPPT_S");
  printf("`----------------------------------------------------------------------´\n");
  do {
    // CIRCUIT SIMULATION
    ret |= bisect_solver(&Vpv, params, fun_circuit, xmin, xmax, tol, maxiter);
    Ipv = panel_model(Vpv, params);

    if (ret != 0) break; // not converged

    // REPORT SIMULATION
    // Note: maybe it needs a clock divider to run in a different frequency
    // other than f=1/delta_time.
    printf("|%- 10.6f|%- 8.3f|%- 8.3f|%- 8.3f|%- 8.3f|%- 8.3f|%- 8.3f|%-4d|\n", 
            time, Ro, Ipv, Vpv, Vpv / Ipv, Vpv * Ipv ,D ,MPPT_STATE);
    send_to_socket(simulation_output_socket,
                   simulation_output_data,
                   simulation_output_data_length);

    // CIRCUIT PERTURBATION
    // Note: maybe it needs a clock divider to run in a different frequency
    // other than f=1/delta_time.
    //Ro += 0.01;  // lOAD PERTURBATION
    D = mppt(Vpv, Ipv); // mppt perturbation
    M = D/(1.0-D);
    Ro = Rl/(M*M);
    static double G_step = 0.1;
    if (time >= 0.002) {
        G -= G_step;
        if(G <= 30) G_step = -G_step;
        if(G>1000) G_step = -G_step;
    }

    time += delta_time;
  } while (time < end_time);
  printf("|------------------------------------------------------------------------|\n");
  printf("| %-9s| %-7s| %-7s| %-7s| %-7s| %-7s| %-7s| %-4s|\n", 
      "time", "Ro", "Ipv", "Vpv", "Vpv/Ipv", "Ppv","D","MPPT_S");
  printf("`------------------------------------------------------------------------´\n");

  return ret;
}

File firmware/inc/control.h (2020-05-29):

#ifndef _CONTROL_H
#define _CONTROL_H


#define P_MIN  3.0f
#define P_MAX  400.0f

#define D_MIN  0.01f
#define D_MAX  0.98f

#define D_STEP_SWAP 0.1f
#define D_STEP_SOFT 0.1
#define D_STEP_MPPT 0.005f
#define D_STEP_LIMIT 0.02f

#define CLK_SWAP 1
#define CLK_SOFT 1
#define CLK_MPPT 1
#define CLK_LIMIT 3

double mppt(double Vpv,double Ipv);
void mppt_machine(void);

void mppt_initializing(void);
void mppt_running(void);
void mppt_soft(void);
void mppt_limit(void);


void swap(void);
void peo(void);
void limit_p(void);

void set_mppt_initializing(void);
void set_mppt_running(void);
void set_mppt_soft(double target);
void set_mppt_limit(void);


enum{INIT,RUNNING,SOFT,LIMIT};

//void set_MPPT_init(void);
//void set_MPPT_running(void);
//void set_MPPT_soft(void);
//void set_MPPT_limit(void);


#endif

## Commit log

2020-04-27 Simple simulator using bisect to solve the circuit.
2020-04-30 Asynchronous unix domain stream socket server implemented
2020-05-01 Client abruptly disconnection solved.
    [main.c]
2020-05-01 Run could clean remaining sockets
2020-05-01 Working socket
2020-08-01 imported MVC hardware
    [analog.sch, atmega328p.sch, basicsensormodule.kicad_pcb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]
2020-08-01 cuk imported and cleared
    [MCC20.kicad_pcb, MCC20.sch, ZCS.sch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]
2020-08-02 Signal and Cuk imported
    [MCC20.kicad_pcb, MCC20.sch, Signal.sch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]
2020-08-02 schematic and footprint
    [12V_supply.sch, MCC20.sch, Signal.sch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]
2020-08-02 sch DRC and THT components position
    [12V_supply.sch, MCC20.kicad_pcb]
2020-08-03 parte de potencia
    [MCC20.kicad_pcb, MCC20.sch]

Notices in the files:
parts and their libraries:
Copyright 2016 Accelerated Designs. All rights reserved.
